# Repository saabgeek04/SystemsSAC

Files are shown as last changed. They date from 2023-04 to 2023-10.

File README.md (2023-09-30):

# Rapid Remote Response Vehicle (RRRV)
This Markdown document details the design process used and the troubleshooting that was involved in creating my RRRV.  
This work was completed as part of VCE Systems engineering Units 3 and 4.  
I wrote this all in markdown for the simplicity and accessability, as well as generally being more pleasant than using word or powerpoint
There are most likely spelling mistakes and grammatical errors in this document spelling is a priority at the moment. I have gone through with a basic spellchecker, but I cannot guarantee perfection.

For my weekly journal, see [here](/journal/WEEKLY.md)

# Overview
## What am I building?
I will be building a remote payload delivery vehicle with a first person view camera. the idea of this vehicle is similar to a bomb disposal robot. Its strength is that it can be used to access areas that are not safe for humans. It will be capable of delivering a payload and navigating complex terrain.  
In more detail, I am going to be equipping my own existing remote control car (Traxxas Slash 4x4) with the equipment needed to drive into an area unsafe for humans so that it can deliver a payload. The car will be run using [Ardupilot Rover](https://ardupilot.org/rover/), and will be able to deposit its payload remotely.  
The payload in question will not be a bomb, I promise. Rather it will be medical supplies or food.  

## Why not a plane?
I'm not designing this for war, but in the event of one, drones and planes can be shot down out of the sky after being picked up on radar. The last thing we want is a urgent and valuable supply drone to fail to complete an urgent mission. A ground vehicle is slower, but could drive along the desert for days on end undetected (and with solar panels too!).  
# Initial Planning and design 
## The Car 
The car is a Traxxas Slash 4x4 VXL
I will be using it as a base, as it has all the features I need and will allow me to focus on the autonomy + Payload. The last thing I need is to be trying to build and diagnose two systems at the same time. The Slash is very robust and reliable, and stands up to large amounts of abuse with ease (trust me, I've tested it). Its also something I am fairly confident with, as I understand it and how it works. Mine has an upgraded steering servo as a bonus as well. 

See [ROVER.md](/journal/ROVER.md) for more information


<i>Picture of the car pre-systems</i>  

## The Autopilot 
I will be using [Ardupilot Rover](https://ardupilot.org/rover/) to automatically drive the car and complete GPS waypoint based missions.  
According to their website:   

<i>Rover is an advanced open source autopilot for guiding ground vehicles and boats. It can run fully autonomous missions that are defined using mission planning software or pre-recorded by the driver during a manual run.</i>

This is perfect for me as I will be able to set up missions around the school to demonstrate the capabilities of my project. 

Documentation for the autopilot side of things will be documented in [ROVER.md](/journal/ROVER.md), as it is all part of designing the rover.

### Background
Ardupilot itself was originally designed as low cost autopilot for remote control aeroplanes and boats, but has also been adapted to run "rovers" as well. Think Mars Rovers. 

It works by acting as a remote control for the vehicle its being used on. It essentially replaces the preinstalled receiver on the "rover". It knows its own position using a GPS module, and connects to a Ground control station for mission instructions and waypoints. 

Overall its a very well sorted system and will make the Autonomous driving part pretty easy (touch wood), allowing me to focus more on the Payload system.

### Hardware
Ardupilot doesn't need much hardware, meaning it will be relatively cheap to install on my car. Below is a brief list of the Hardware I will need:  

- Ardupilot control module
- GPS module
- Telemetry/control TX/RX system
- Sonar/IR for obstacle avoidance (maybe)

See [This Section](/journal/ROVER.md#navigation-computers) for which exact bits I used and why.

### Software
I will be using [Mission Planner](https://ardupilot.org/planner/index.html#home) for my Ground Control Software (GCS) as it is the most supported and popular GCS for Windows. 



As you can see in the screenshot above, Mission planner will allow me to create a set of waypoints which my rover will use GPS to navigate to. Mission planner will also be able to show my FPV camera footage in its HUD if needed, but I could also do a VLC stream if I needed.

## The Payload

See also [Payload System](/journal/PAYLOAD.md)

My initial ideas for the payload so far have been to deliver a cylinder about the size of a 600ml water bottle or maybe a pringles can. The payload will be secured to the vehicle via a custom designed clamping system. I am considering using a seatbelt style strap + tensioner as well, which would allow me to secure multiple types of package. 

### A Cylinder? Why not a box
I am choosing to use a cylinder for a couple of reasons, primarily because they are very easy for a human to hold due to the shape. It also gives me a fun engineering challenge in terms of securing it as it is more complex and less conventional compared to a box. A cylindrical payload could also be transported via other methods, and would be far better for transporting liquids for human consumption (who knows, someone could really really need a bottle of mount franklin!). 
### Securing the Payload

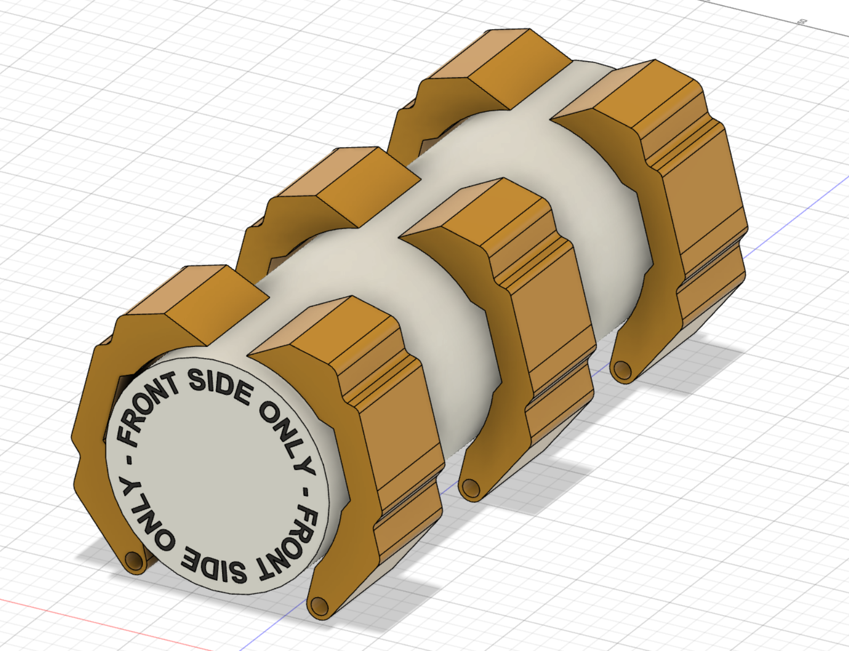
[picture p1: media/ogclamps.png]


I am going to use a clamping system to secure the payload to the vehicle. I want this system to be adaptive to the size/shape of the payload, allowing shapes like water bottles to be held firmly in place. I will have 6 clamping arms along the long side, with another thing at the end to prevent sliding forwards and backwards. The front side will be pressed up against part of the vehicle.

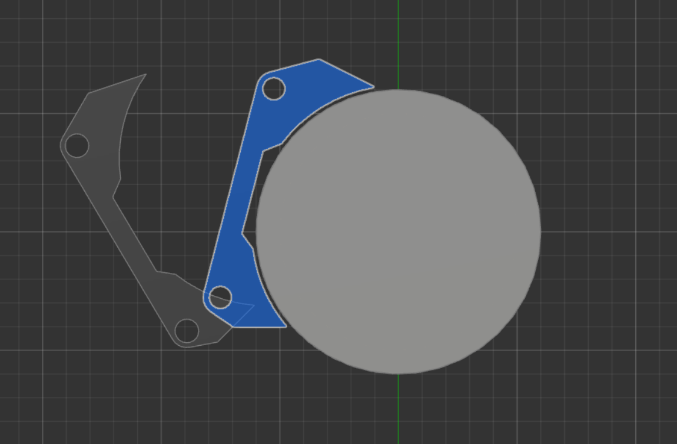
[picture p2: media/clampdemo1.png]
  

<i>Demonstration of initial clamp design and its pivot point</i>

Ideally the clamps can move independently of each other, allowing the greatest flexibility. This does present a problem however: how do I move all 6 (or 3 pairs of 2) at the same time, without needing 
6 individual motors?

I continue the design process for this part in the [PAYLOAD.md](/journal/PAYLOAD.md) document.

## Risk Assessment

As with any project, there are risks involved with the operation of this rover. To help identify and mitigate these, I have grabbed the risk assessment matrix from the [Worksafe website](https://www.worksafe.vic.gov.au/how-conduct-risk-assessment) and filled it in with colours to make it nicer to look at 

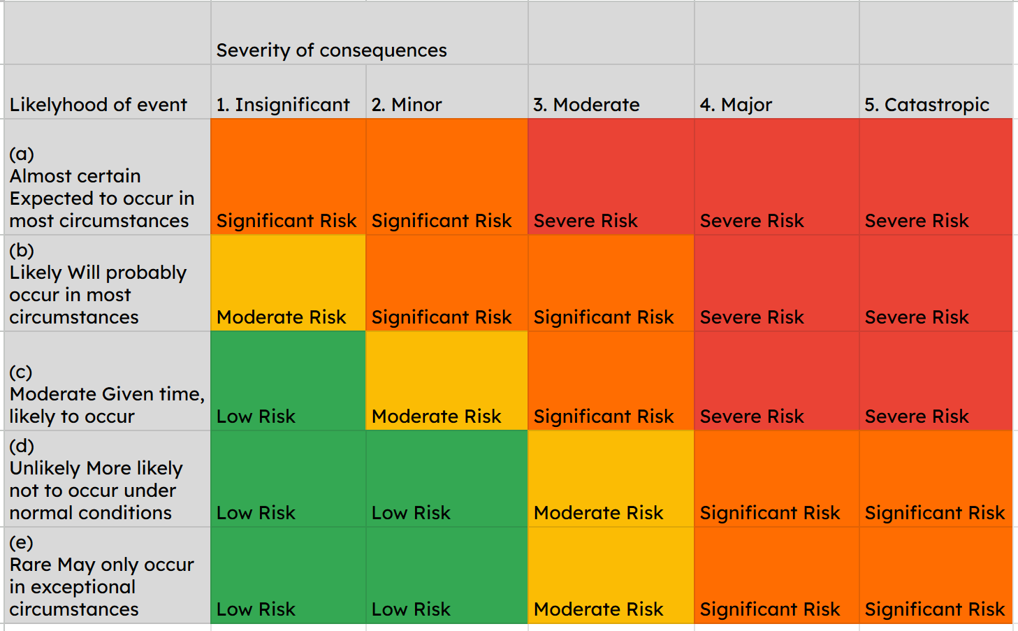
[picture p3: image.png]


#### Key

##### 1. Insignificant
Any injury or disease that needs first aid treatment only.
##### 2. Minor
Any injury or disease that is likely to result in a person being incapacitated from normal activity for a continuous period of up to 7 days.
##### 3. Moderate
Any injury or disease that is likely to result in a person being incapacitated from normal activity for a continuous period of 7 or more days.
##### 4. Major
A fatality or total and permanent disability.
##### 5. Catastrophic
Multiple fatalities.

So, what are some of the risks we might run into? 

### 1. The Rover collides with a person

#### Likelyhood: Unlikely
It would take very strange circumstances for the rover to collide with a human. Humans tend to see it coming and move it out of the way. Unless you somehow dont see or hear it coming (from quite a while away). Its very easy to detect.
#### Severity: Insignificant
I have had the rover collide with me alot. I have sustained less than a bruise from these collisions. It kinda just bounces off your feet.
#### Verdict: Low Risk
A possible solution would be the Lidar sensor to get the rover to avoid humans.

### 2. The Rover Battery Explodes

#### Likelyhood: Rare
The Lithium-Polymer (LiPo) battery used to power the rover is very unlikely to experience thermal runaway during operation. The Flight controller knows the battery percentage, and will trigger a safety toggle to stop operation. The risk really comes from charging the battery, but if the battery is charged on a safe charger and the balance lead is used, then there is virtually no risk of a fire.
#### Severity: Moderate
A LiPo battery explosion is pretty violent. Theres alot of heat that gets released very quickly. If the battery is close to a human whilst charging, then they could get seriously burned.
#### Verdict: Moderate Risk
I believe as long as the LiPo battery is treated with respect, and the user understands how to identify a battery that is at risk, then the risk will be minimised.

### 3. Manual handling of the Rover resulting in back injury

#### Likelyhood: Moderate
Someone in a rush may use improper lifting techniques to lift the Rover.
#### Severity: Minor
Gets worse over time but on a single occurance factor could be unpleasant.
#### Verdict: Moderate Risk
If the correct lifting procedures are followed, then injury will not occur.

### 4. Rover motors activate whilst the rover is being handled, causing harm

#### Likelyhood: Unlikely
It has never ever happened to me, and I've done a bunch of dumb stuff with the rover
#### Severity: Insignificant
The most that would happen is you might get a bit of carpetburn from one of the tires or a pinched finger
#### Verdict: Low Risk
A saftey switch to kill motor power is installed on the rover to prevent this from happening.

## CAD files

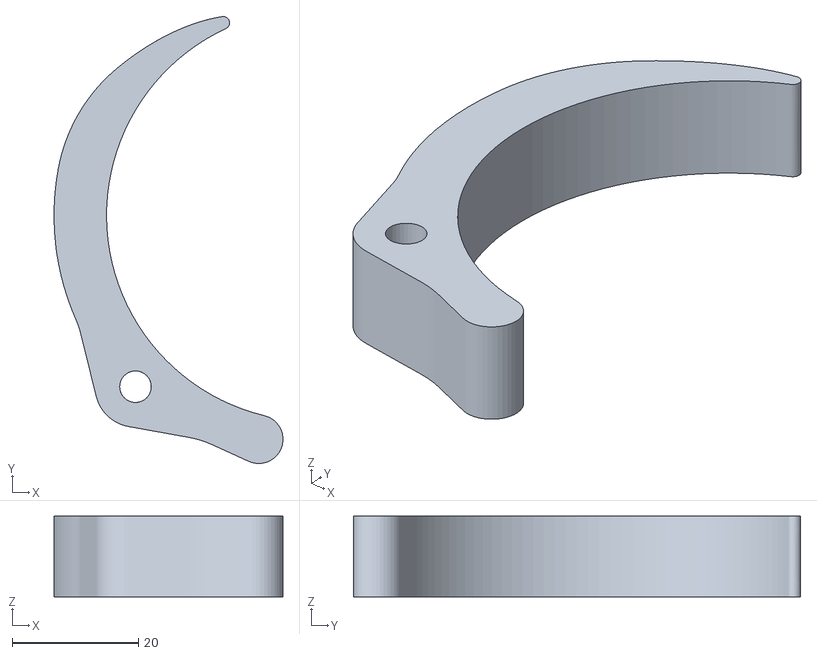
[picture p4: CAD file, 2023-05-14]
3D models/stl/clamp.stl
36.2 x 70.7 x 12.8

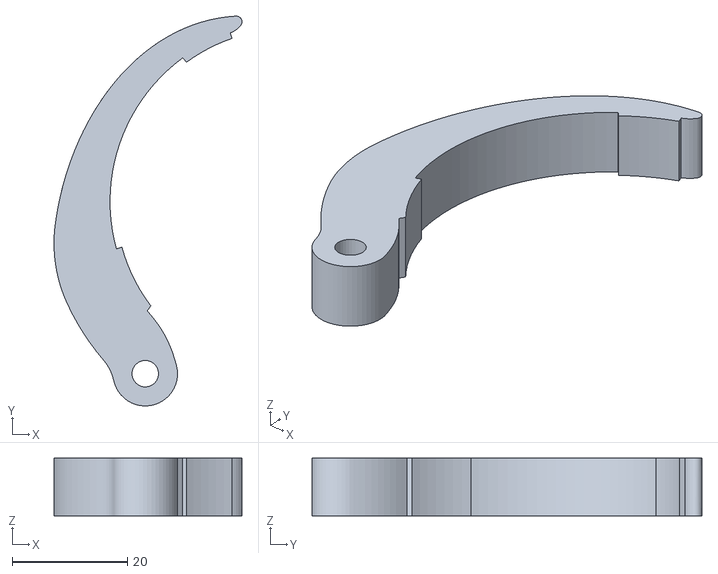
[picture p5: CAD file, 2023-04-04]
3D models/stl/boringclamp.stl
32.7 x 67.7 x 10.0

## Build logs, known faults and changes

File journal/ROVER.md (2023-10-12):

#### [< Back to README.md](/README.md)

# Rover Building
This document details the process I followed to turn my Traxxas slash into a autonomous rover.

## Initial Planning and designs

The Traxxas Slash, like most hobby class remote control cars, has a flimsy plastic body that attaches to the chassis via 4 mounting poles. The body is non structural, and mostly serves as a protective cover, allowing crashes and rollovers to occur without damaging the vehicle. It also has front and rear bumpers, as well as side bash bars, for maximum safety. 

Ideally, All modifications added to the car are completely reversible, "bolt on" modifications.

I initially wanted to mount the navigation equipment in place of the body, via attaching a plate to the four mounting points. I tested this, and found it was not a bad solution. The car drove fine with the plate installed despite the increase in center of gravity, However there are a couple of issues with this design, the main one being that the navigation system would not be protected in event of a rollover, (which would be more likely due to the increase in CG). The other issue is that the body mounts are not designed to deal with the huge forces that I would be creating with all the extra weight.

I then came across this [forum post](https://diydrones.com/group/ardurover-user-group/forum/pixhawk-equipped-4wd-traxxas-slash-chassis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) which basically solves all my problems. 

As you can see in the following images, The navigation systems are mounted on a plate much closer to the chassis.

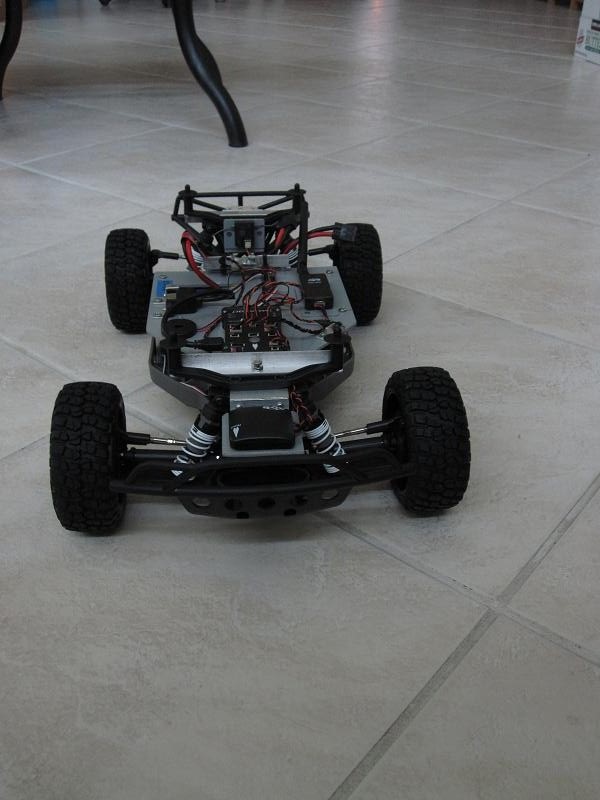
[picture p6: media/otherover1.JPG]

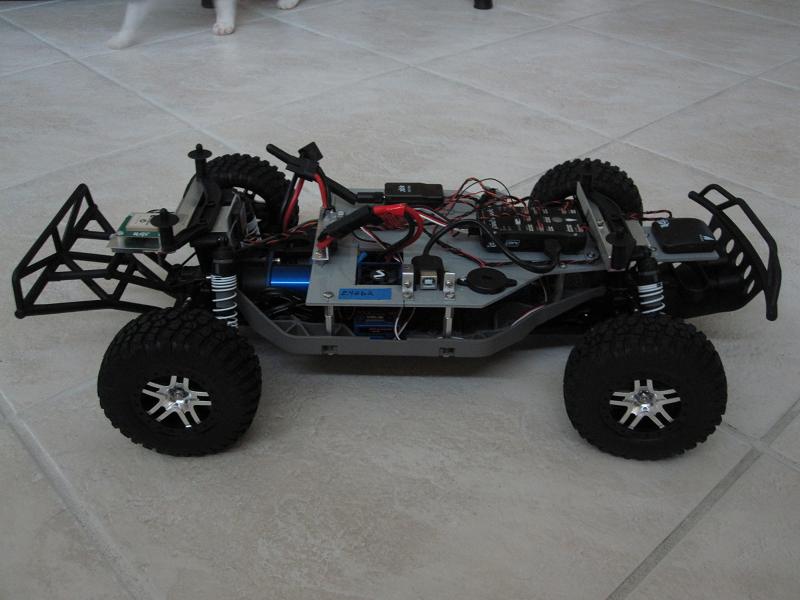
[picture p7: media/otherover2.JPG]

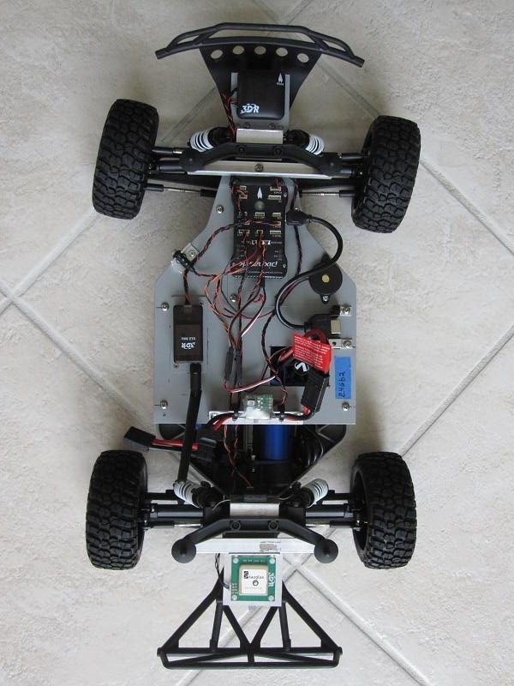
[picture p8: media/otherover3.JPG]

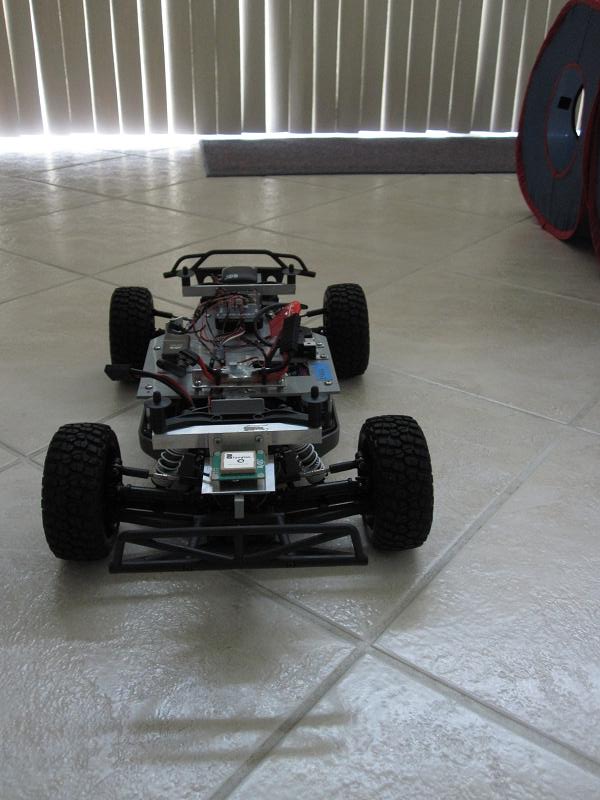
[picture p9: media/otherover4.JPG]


This is a far better design then what I was going for, so Credit to [Thomas J Coyle III](https://diydrones.com/members/ThomasJCoyleIII) for that. 
I will be attempting to reverse engineer these designs so I figured credit was a good idea...

I will be laser cutting the navigation plate out of acrylic, which will mean I can be very precise in the nav mount design. 

I plan to construct two versions, one for prototyping, and one as the final design. This will allow me to figure out exactly which electronics and computers I need without worrying about space on the rover, before constructing the most efficient plate, saving weight and space 

## Navigation Computers

As I previously mentioned when talking about Ardupilot, I needed a couple of pieces of hardware to make my car into a rover

- Ardupilot control module
- GPS module
- Telemetry/control TX/RX system
- Sonar/IR for obstacle avoidance (maybe)

### Which to buy on a budget?

The control module is the bit that makes everything happen. It plugs into the speed controller and steering servo to drive the rover, as well as receiving GPS signal from the GPS module.

The ideal system, if available, would be the [Pixhawk 4](https://holybro.com/products/pixhawk-4?variant=41527199498429), which is unfortunately out of stock and very expensive. Its also a bit overkill for what I need, since I am using a rover and not a drone/aeroplane with complex shenanigans going on.

I started looking for a cheaper flight controller and eventually found a kit on aliexpress that for the price of a regular Pixhawk, would give me all the hardware I need + a Pixhawk clone, as a bunch of bonus bits. [This is the kit](https://www.aliexpress.com/item/1005005167479286.html) and I plan on purchasing the "915V1 1000MWPackageC" Variant. I know I said earlier that I didn't need all the functionality of a fully fledged Pixhawk, but I couldn't really find a better kit for the money. 

This variant comes with a cable that has a voltage regulator built in to power the Pixhawk clone, meaning no cable splicing is required. It also features 1000mw 433mhz radio, which will do the job. 433mhz is not as fast as regular 2.4Ghz, but for my application it will be fine. The 1000mw rating means I will have plenty of range too. Originally I planned to use a 933mhz system, but due to legal requirements I cannot. The power limit for 433mhz is only 25mw ERIP, the ERIP of my radio system is about 100mw, so I'll just turn it down a bit :wink: 

The included GPS module may not be very good, but I happen to have a large box of GPS modules, which were used 20 years ago for mapping and surveying large areas. They are fitted with USB connectors currently, but I can always solder different connectors on if required. I plan to stick with a single GPS unless I start having issues. 

The kit also contains a safety switch (basically a big red emergency stop button but without the big and red parts), a buzzer that can be enabled if the rover is lost and a sd card to be used as a rudimentary "Black Box".

I think this kit, which at this time is on sale for $335 is the best option for me at the moment. Obviously, in an ideal world I would not have to worry about cost and I would just spec out the best solution for this, but I don't have that luxury (Someone sponsor me!) so I'll be doing this all on the cheap, which is kind of the wrong way around if you think about the RC car I'm using as a base. 

There are a couple of other options that are cheaper, but they miss out on certain sensors like a compass, which I may need, and I would hate to order the cheaper kit and need a compass or something else and have to spend more money + time getting a new kit. Once I sort everything out, I will write out a set of minimum requirements so that anyone can spec out a system that works for them for a better price.

## Designing the Navigation platform 

Whilst I wait for the Navigation computer to arrive, I will begin designing the platform for everything to reside on. At this point in time, since I am away, I do not have access to the car itself, but I have previously measured out parts of the car that I can then combine with an arial shot of the car to get approximate measurements. When I return home I will be able to take some more precise measurements of the car to further refine the model. I know that I am not the most precise measurerer, so I will build in adjustability in form of some slots. I will also cut prototypes out of cardboard to make sure everything fits properly without wasting material (a mistake I made previously...oops)
To create the initial plan design I traced a top down photo of the rover chassis, not very precise, but I can tidy it up later

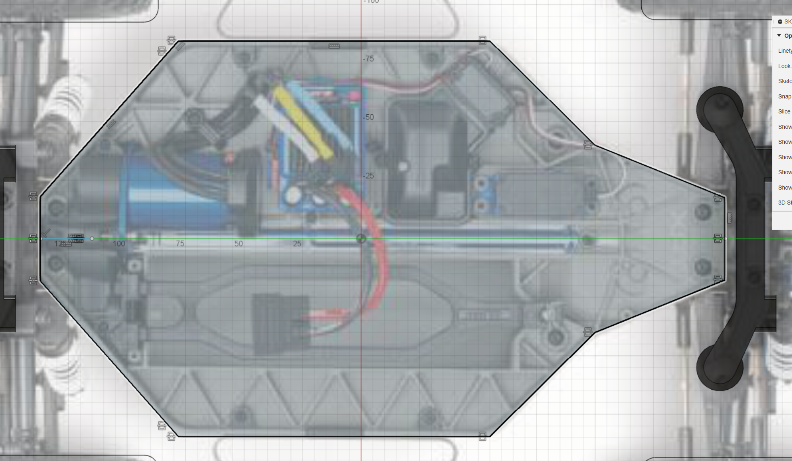
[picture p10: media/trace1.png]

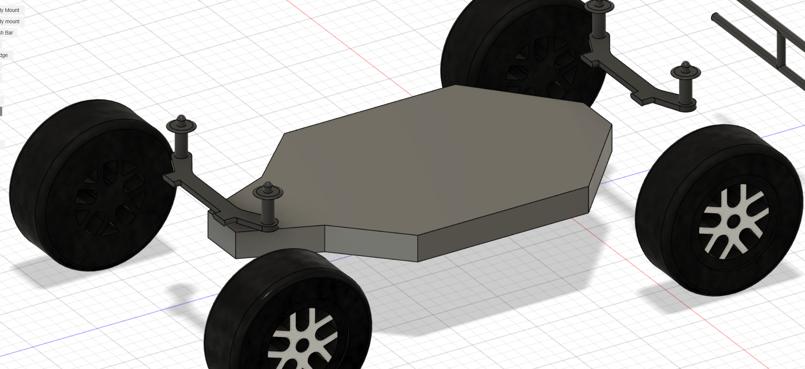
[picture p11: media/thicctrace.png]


I did this on the same document I used to make [this acrylic plate](/journal/WEEKLY.md#23rd-february) as the measurements for the body mounts were somewhat accurate (+-1.5mm). When I have access to the rover in person again, I will be able to measure out the length of each side and draw a new sketch to suit.

There are alot of different forces at play during rover operation, and I want the computers to stay relatively safe during this. I expect to hitting lots of bumps and other obstacles, and even if I do upgrade the suspension, theres only so much it can do to smooth things out. The primary computer comes with a anti vibration mount, but the rest of the stuff does not, fortunately, we can 3D print TPU (a kind of rubber), which I will use to make rubber "washers" that will soak up a decent amount of vibration.

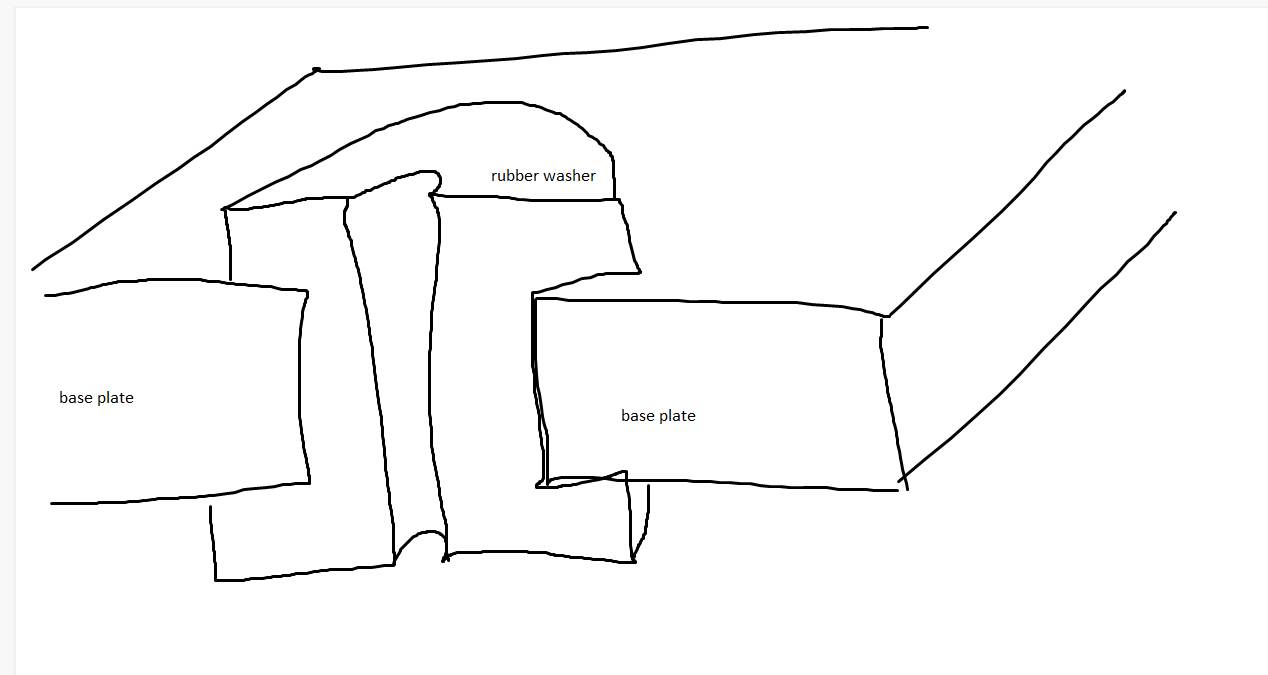
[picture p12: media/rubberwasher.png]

<i>an expertly drawn cross section of the rubber washer design</i>

When I got back from WA, I measured out the exact(ish) dimensions of the chassis, which was difficult without removing parts of the car but I managed to do it.

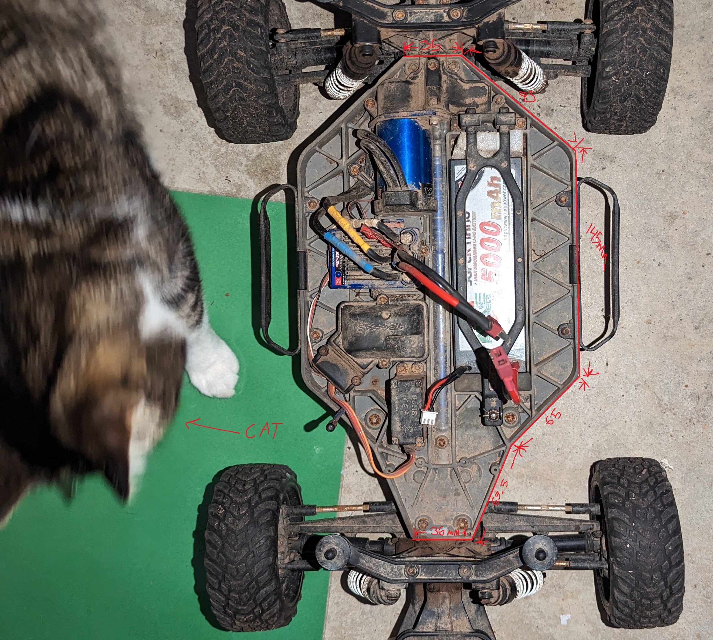
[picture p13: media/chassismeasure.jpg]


Its not the greatest of photos, but it doesn't need to be either.

I struggled to get everything to line up, but then I got the width and length measurements and that helped alot with sorting out everything. I wasn't sure what angle the 65 and 63.5 bits were on, so I made circles with the same radius and used the intersecting point of those two circles, which worked very well!

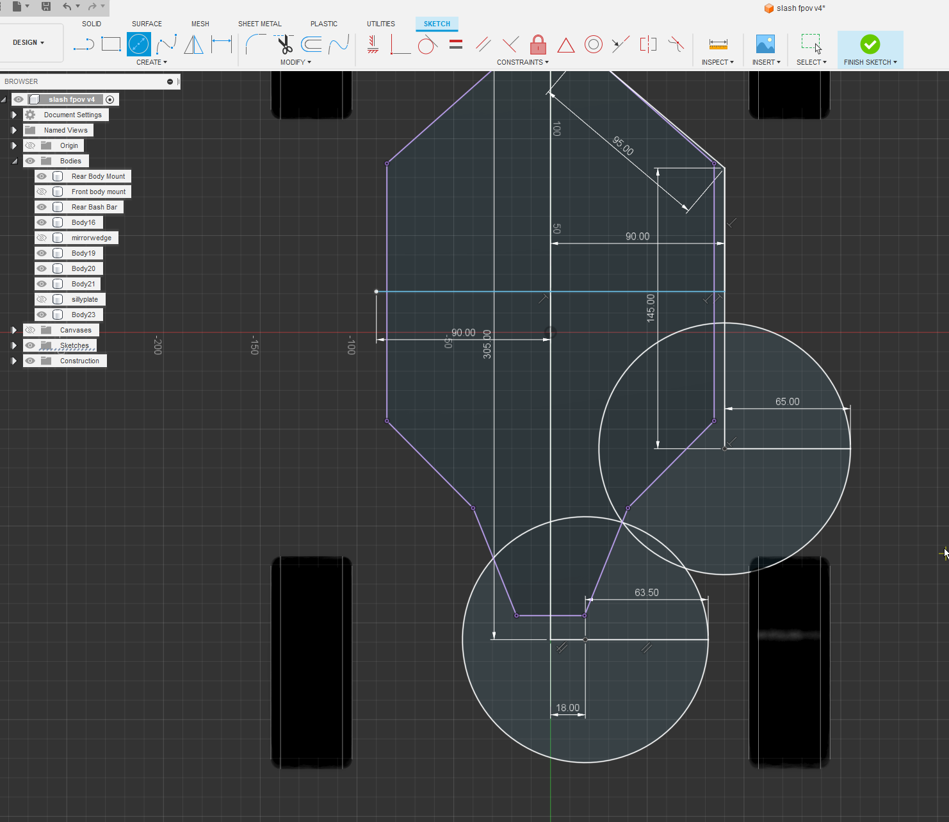
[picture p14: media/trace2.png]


In this next image, the blue is the old one and the grey is the new one, as you can see 

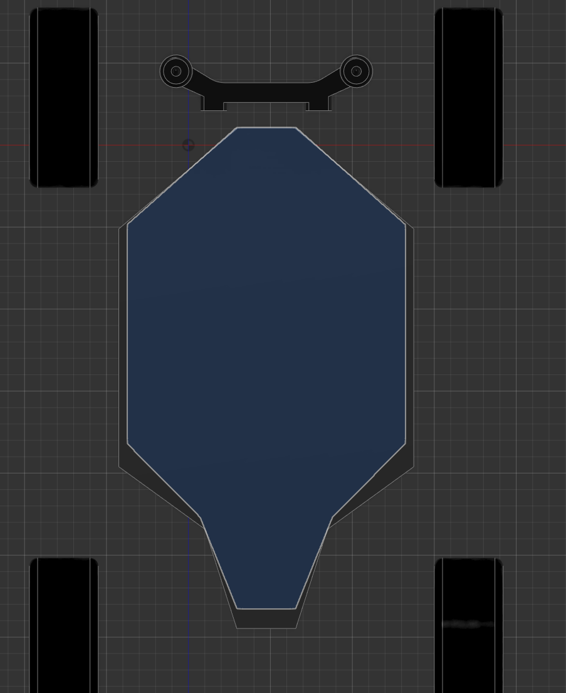
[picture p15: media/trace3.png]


In class, I cut this trace out using cardboard, and no suprises here, it didn't fit properly. I went through 5 iterations, every time getting closer and closer to perfection. I still need to make the 5th piece narrower at the back, that way I can accommodate the suspension. The laser cutter we have is amazing for rapid prototyping in this instance, as I can cut, review and redesign over and over, all using cardboard that would have otherwise been thrown away.

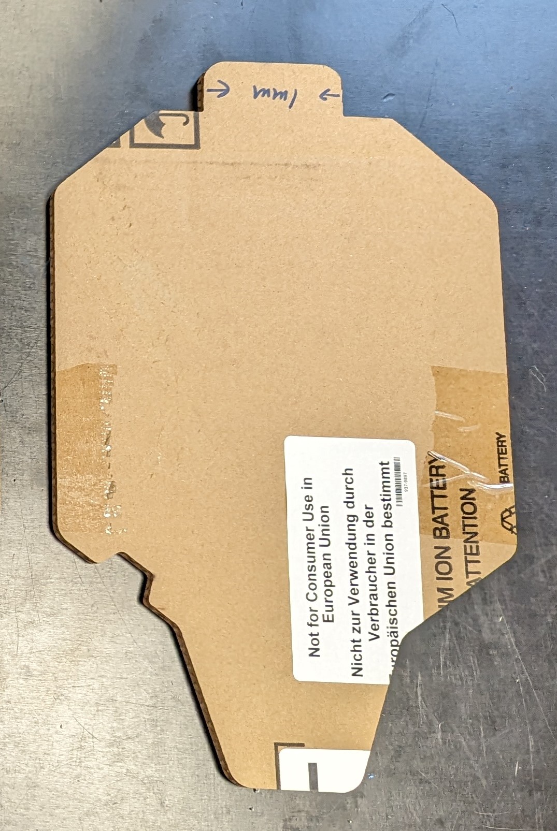
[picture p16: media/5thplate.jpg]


## Flight controller setup and usage

Getting the Pixhawk working was pretty easy. It seems complex initally due to the amount of stuff going on, but once you understand everything its not bad at all. 

[](image-1.png)

<i> A diagram showing all the devices connected to the pixhawk</i>

When I got my pixhawk, I was instructed to put particular firmware on it, so I did, and it didnt work at all. I put the latest firmware on it and it started working. There wasnt much else to do except mount everything. Most of the stuff I had to do to get it to work properly was PID tuning and Motor Calibration. 

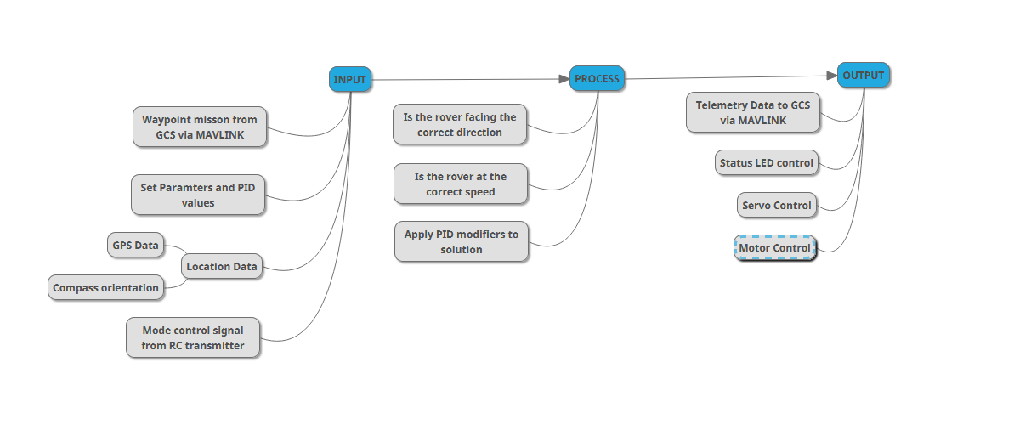
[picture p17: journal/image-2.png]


## Complete Redesign

I realised it wasnt super efficient or really worth mounting everything on a single plate, and I also wasnt happy with the mounting system at all. I made up some parts in fusion360. The idea with these was to make my mount alot stronger and less wobbly, reducing stress and enabling me to mount things better. 

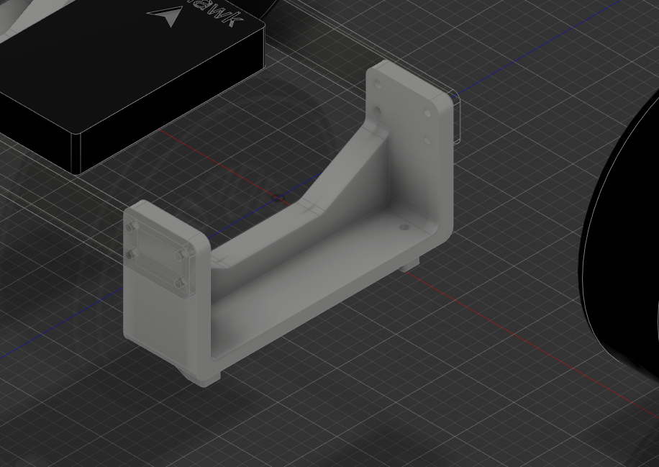
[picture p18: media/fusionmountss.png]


I then 3d printed these pieces, one at a time due to the dubious reliablility of the 3d printers. 

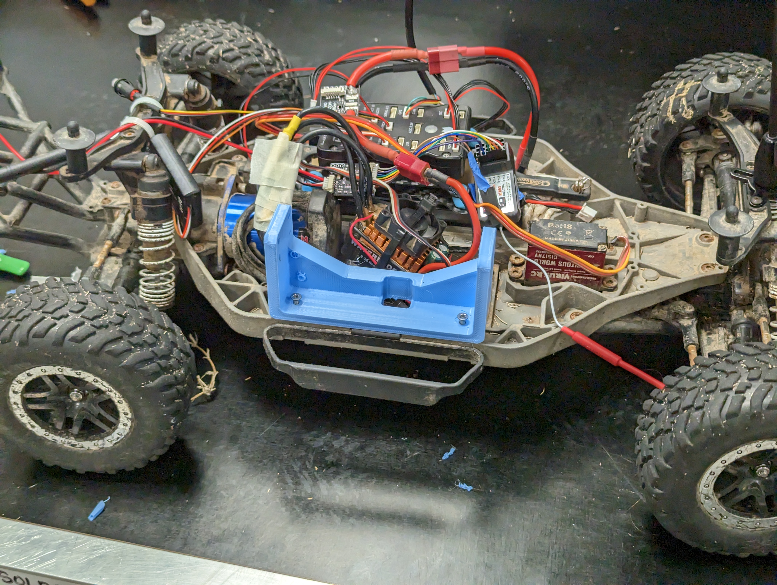
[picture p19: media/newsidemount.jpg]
  
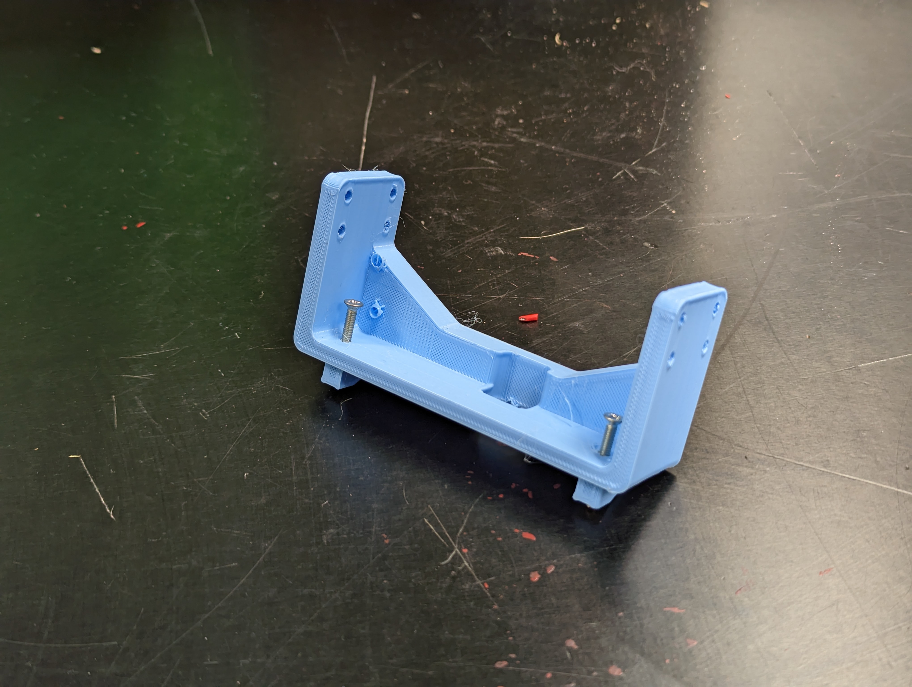
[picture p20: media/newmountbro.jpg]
  

Notice that the reciever and ESC just floating around in the car. I ended up making a mounting plate 

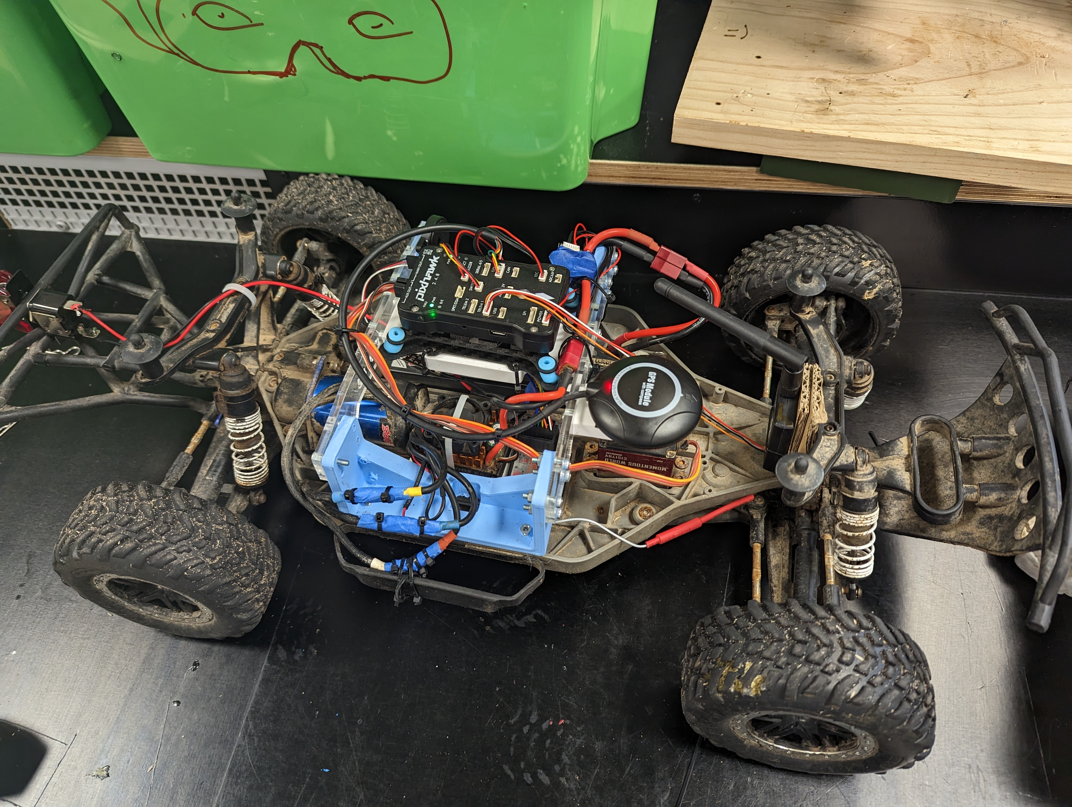
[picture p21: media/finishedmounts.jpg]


This week, I finished printing the other mount and laser cut some cross braces. I built holes into the cross braces, that way I could mount the pixhawk and I also lowered the GPS. I was initially concerned about the GPS getting less reception due to being down lower, but in practice, this was not the case. On occasion, I noticed I had one less satellite, so no really huge difference there

I also mounted the speed controller and reciever much lower and properly wwith 3M DualLock velcro tape, which works really well.

After some brief testing, I found that I needed to make some mudguards to stop grass and mud entering the rover. I prototyped some parts out of cardboard, which worked pretty well and got rid of 99% of the debris, but the cardboard was not going to last very long, see below:

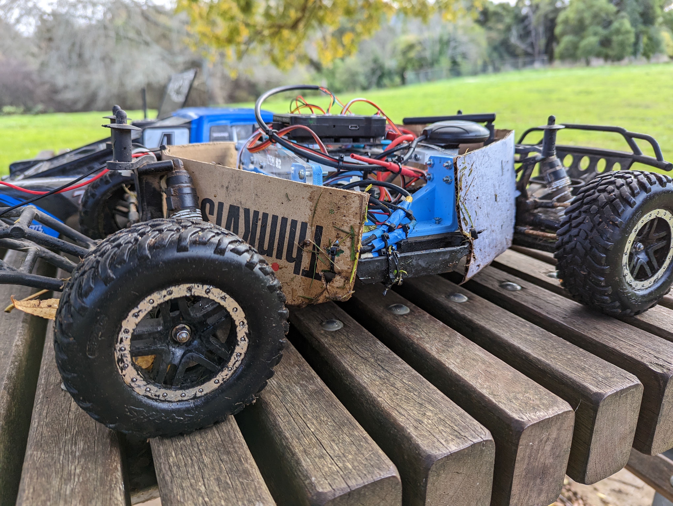
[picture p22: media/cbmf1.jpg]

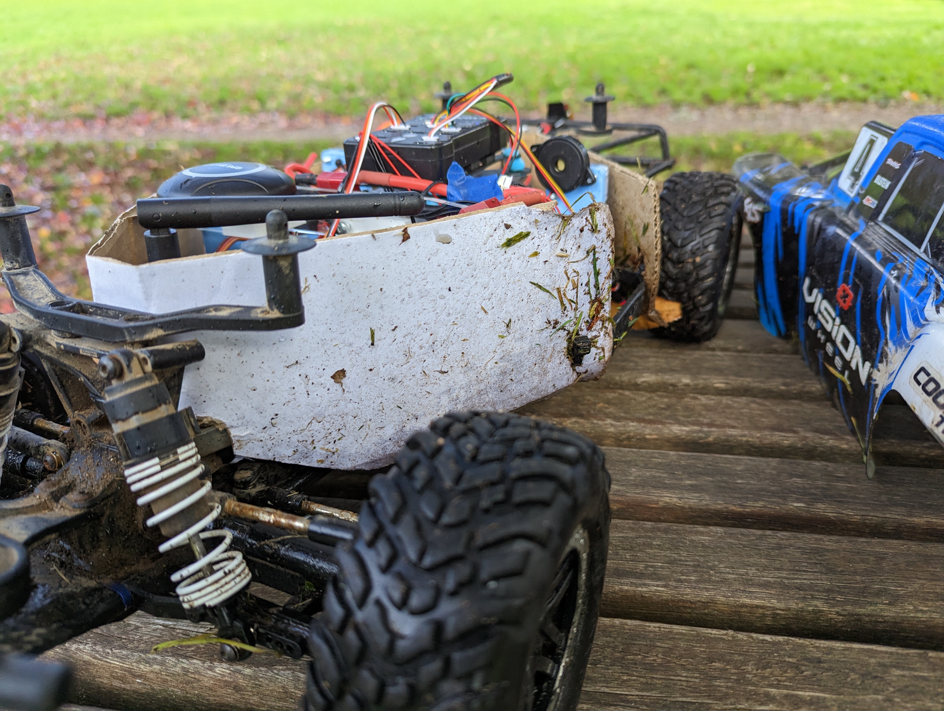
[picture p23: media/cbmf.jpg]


To fix this, I made some new parts out of coreflute. These look much cooler, and dont get saturated when used in water. I still have some water hitting the underside of the "cabin" portion of the body, and this can cause water to drip down into the "isloated" space where the electronics are, so I am going to look into getting a waterproof mesh cover or something similar. If I wanted everything totally waterproof, then I would probably put everything in a tuppawere container, but this is not a boat, so I should be fine.

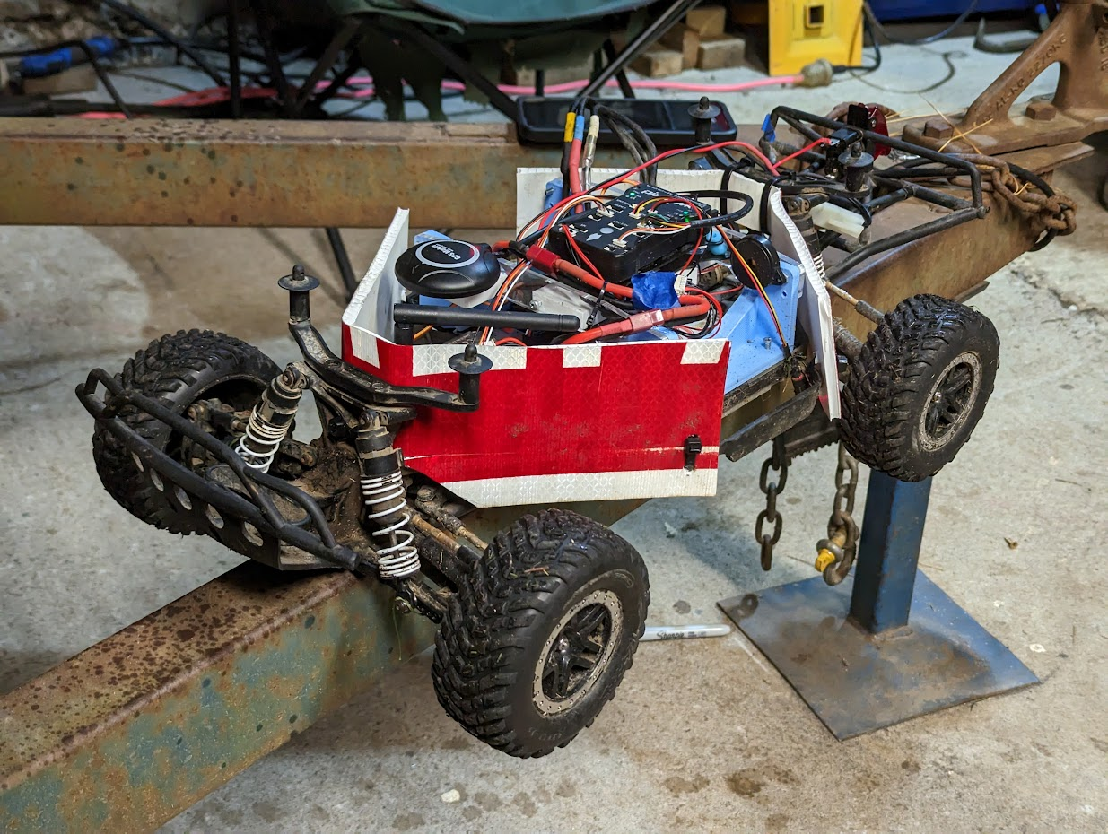
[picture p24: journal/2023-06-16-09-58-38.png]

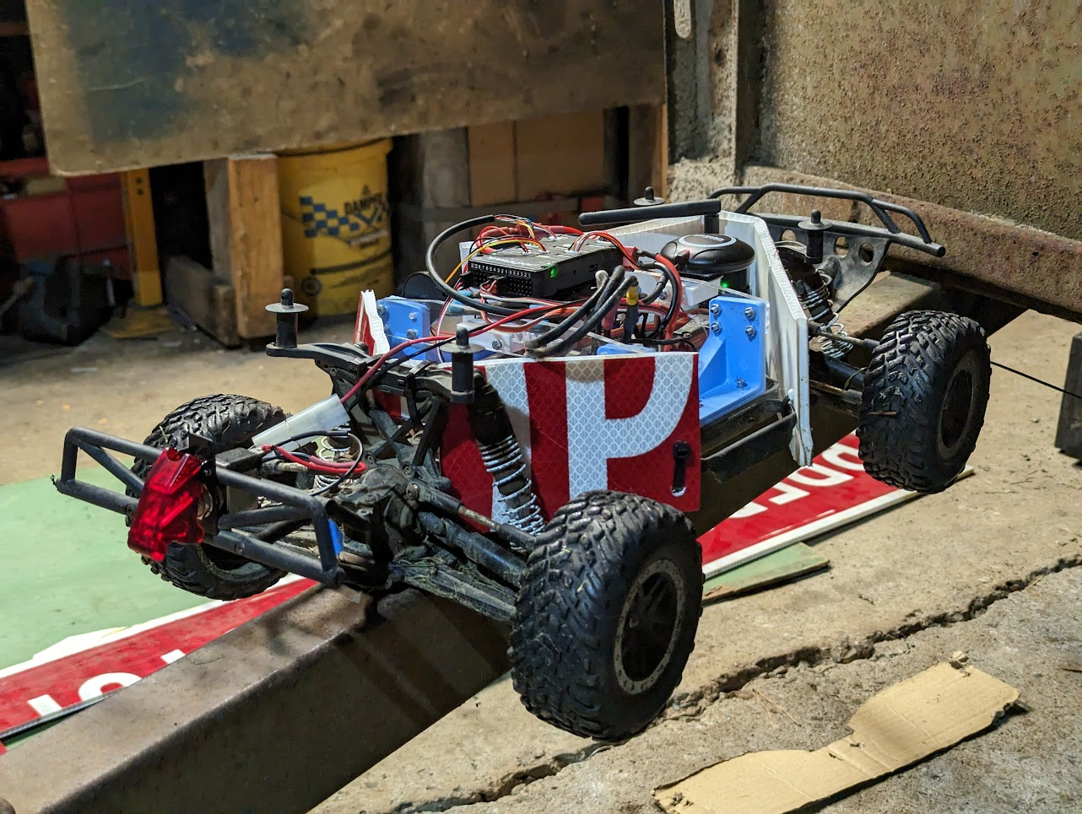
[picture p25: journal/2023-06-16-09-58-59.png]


This was also done on relatively tall, wet grass, which is difficult for a whole host of other reasons.

### Final layout

Heres a little collection of photos showing the final layout of parts on the rover

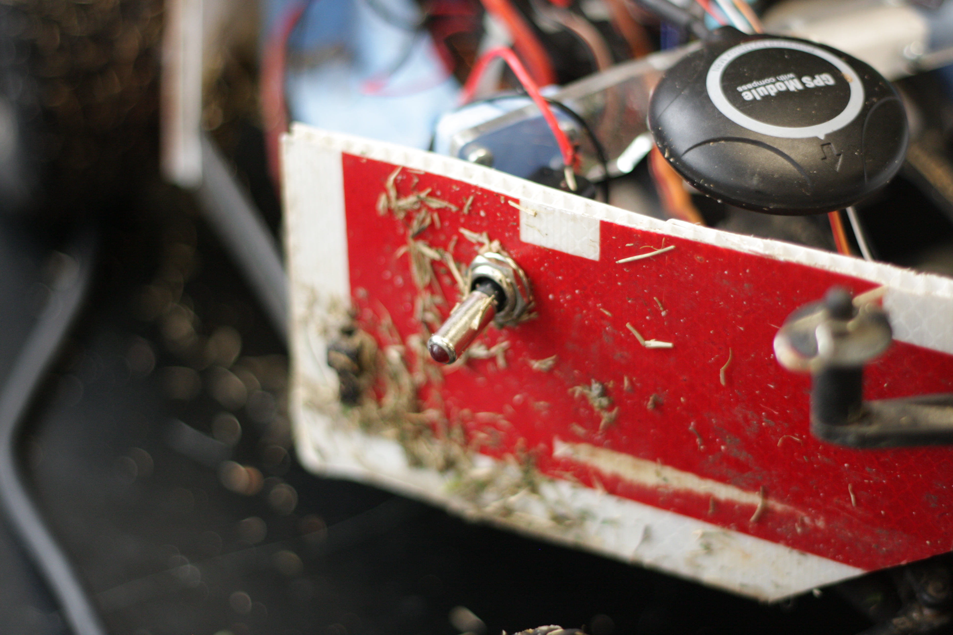
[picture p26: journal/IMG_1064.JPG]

*The GPS and Motor Shutoff Switch*

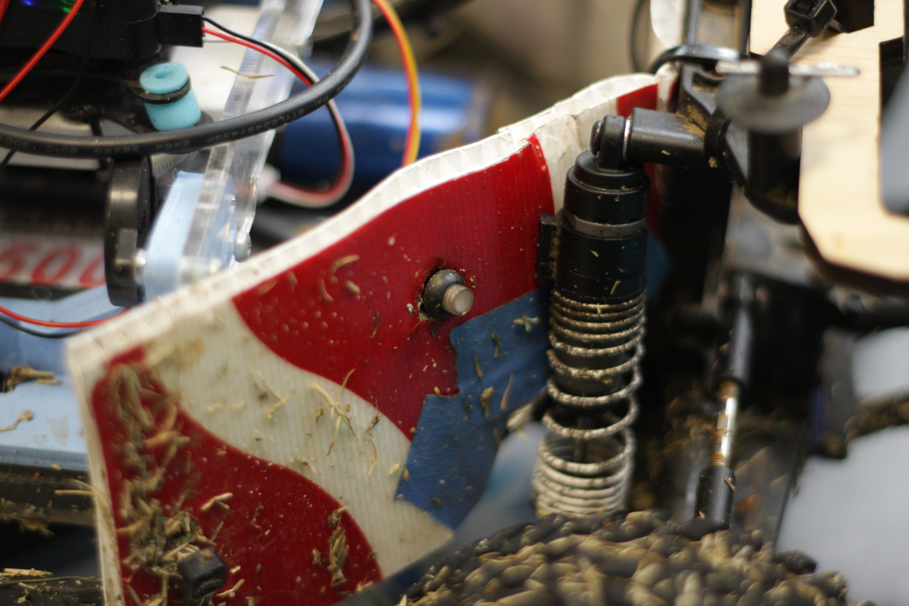
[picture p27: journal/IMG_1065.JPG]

*The Safety Switch at the rear of the car*

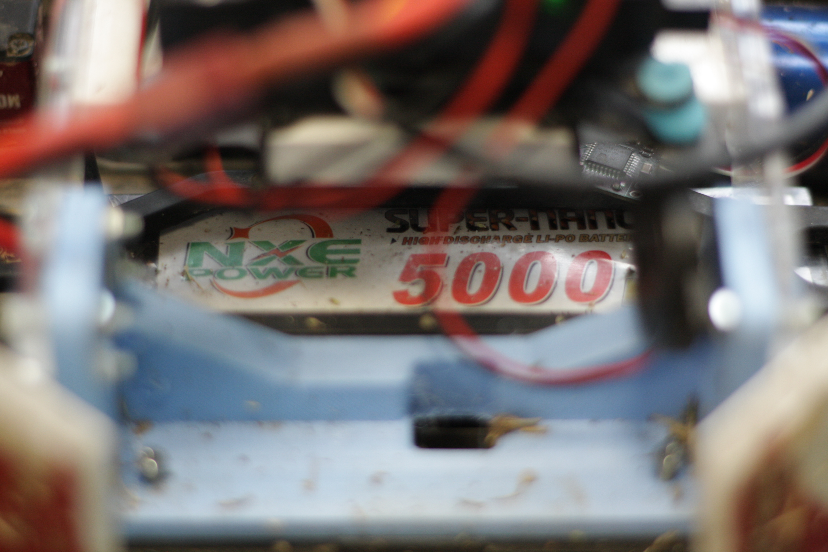
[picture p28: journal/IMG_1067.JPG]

*The battery tucked away in its compartment. At the top-right, you can see the PPM encoder*

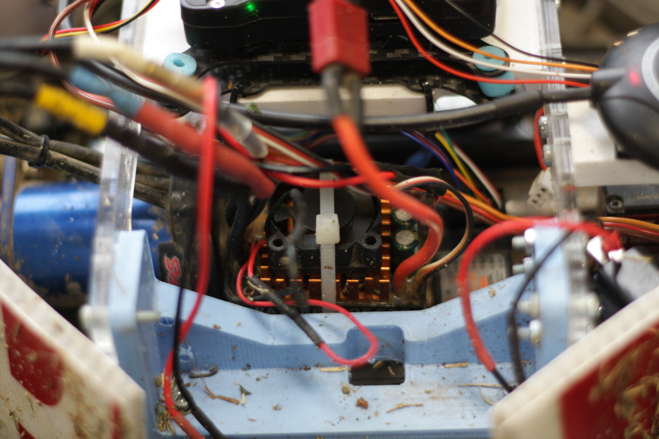
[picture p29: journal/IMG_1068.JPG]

*The Electronic Speed Controller (ESC)*

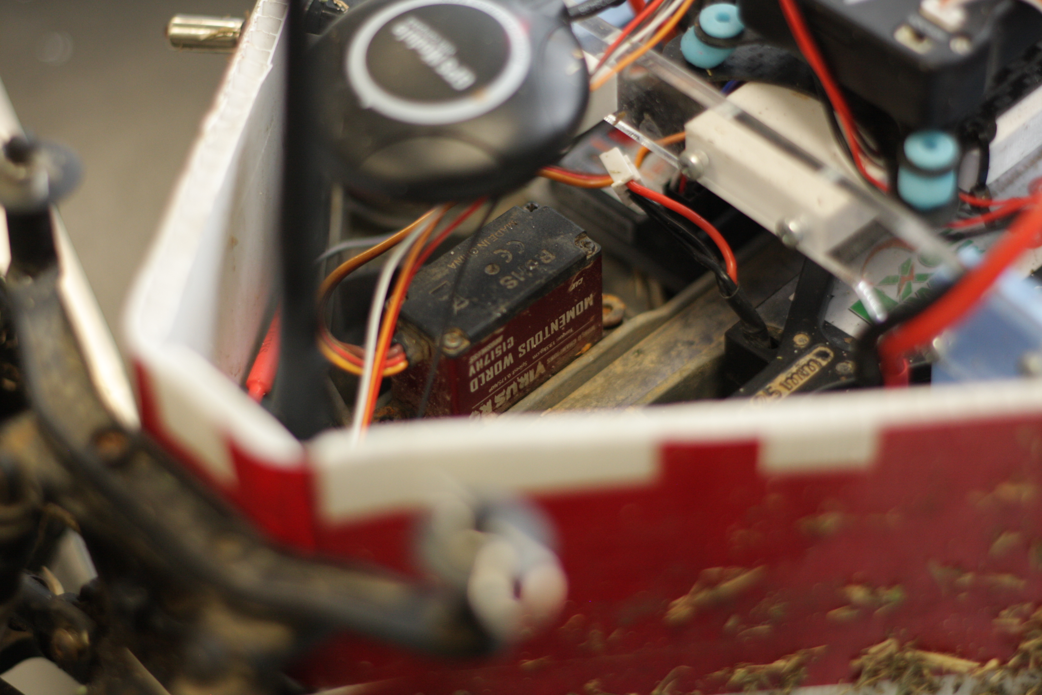
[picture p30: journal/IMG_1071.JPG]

*The Steering servo sitting up front*

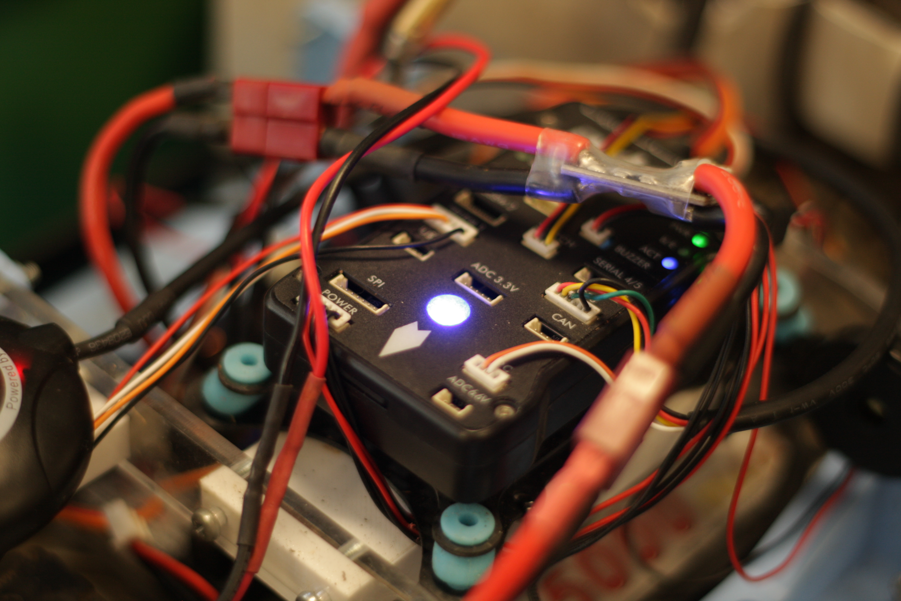
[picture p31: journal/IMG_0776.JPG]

*The Pixhawk, I.E the brains of it all*

## Lightbar 

I really wanted to have a lightbar that woudl show me some status lights as well as work as navigation lights at night. The Ardupilot actually has support for profiLED and neopixel LEDs, but if you wanna do fancy stuff with them like I do, you actually need to write some lua scripts. I am by no means any good at programming. To date, the most I've done is make a javascript... script? that rotates a window on a website to face the cursor, very similar to a steam trading card. 

I looked at some example code, and with the help of a much more skilled friend, went through and we tried to make a script that would work. After about 4 hours of troubleshooting, much refactoring and 2 new wiring harnesses, we gave up on profiLED.

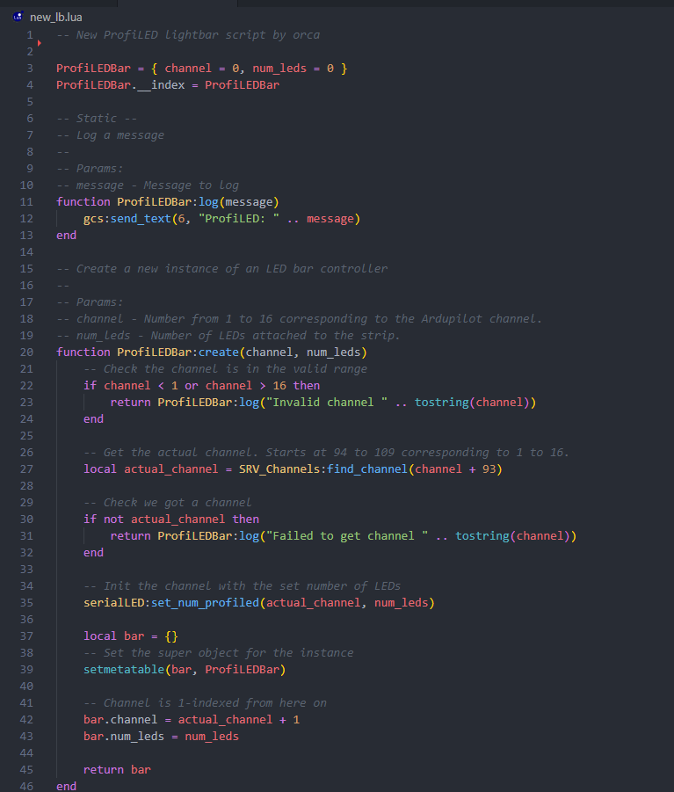
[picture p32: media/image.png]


<i>part of the code we wrote</i>

I then tried using Neopixels instead, but could not get any output out of the Pixhawk at all.

## Obstacle avoidance and LIDAR

I had a little budget left and really wanted to have obstacle avoidance, so I spent $80 and bought a TF02 Lidar sensor off aliexpress. It suprisingly only took two weeks to ship, and when it arrived I had to repin it, but once that was done I plugged it in, set the relevant parameters and.... nothing. It was getting pretty annoying having nothing new work with the Pixhawk, sooo...

## Firmware

It was at this point I decided to reflash the firmware on the pixhawk. I backed up all the parameters and reflashed Ardupilot rover onto it. This fixed nothing. This kinda sucked. I had a look at other options for Pixhawk firmware as well as different GCS (ground control software). I landed on running PX4 firmware (as opposed to ardupilot, which I was previously running) and using [QGroundControl](http://qgroundcontrol.com/). This combination seems to be more of an industry standard(?) and is the "it just works" solution compared to ardupilot, which is more of a hobby class solution. I haven't started on getting LIDAR or the lightbar working on Qgroundcontrol, but currently, I'm happy that its just working, and the user experience on Qgroundcontrol is much nicer than Ardupilot. It's highly likey that my issues with LIDAR and NeoPixel are due to me purchasing a flight controller off aliexpress, but its worth trying all the software first before I come to that conclusion. 

## Ground clearance

You may have noticed that the rover sits pretty low, which is great for handling and driving at speed, but I found that now that I have a payload on the vehicle, the rear sits way too low, and over bumps can hit the ground pretty hard I rebuilt the rear shock absorbers to help with this, (I may or may not have blown them out at the skatepark last year and forgot to put new oil in them...). I initally put a blend of 10w and 85w oil in to try and achieve something close to 45-50w, which is whats reccomended for this model, but this ended up not being quite enough. The thicker the oil in a shock absorber is, the slower it moves. I ended up putting 85w in for this reason, as well as moving the shocks into a more vertical position, meaning that the rover was nice and high off the ground.

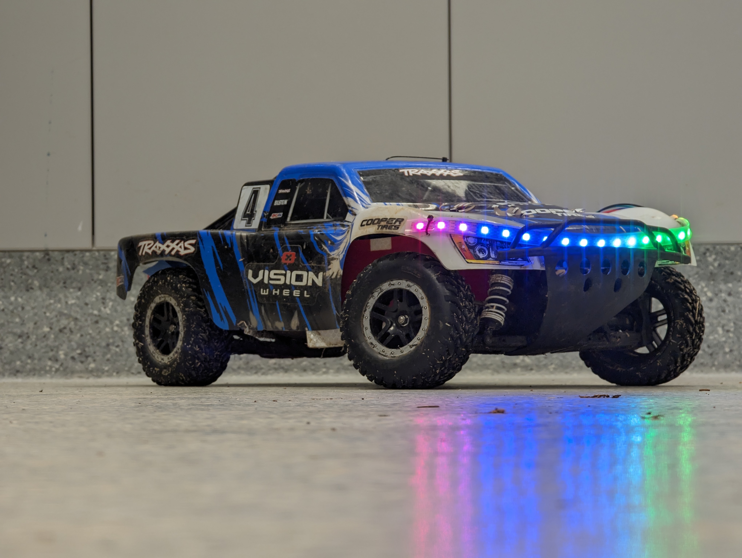
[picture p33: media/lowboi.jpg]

<i>Old suspension config, No Payload... when the profiLED bar kinda worked</i>

#### insert images here of new suspension.

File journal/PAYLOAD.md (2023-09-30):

#### [< Back to README.md](/README.md)

# Payload Clamping System
This document details the design process I used to create the Clamps system that will secure my payload. 

## Initial Designs 



I designed the initial clamps whilst on a plane to western australia, and all they really do is grab the payload and pull it down. They were very simple clamps but they worked, somewhat. I was sitting next to my dad on the plane, so him and I discussed the clamps and their shape quite a bit, and we started focusing on shape optimization.

With my dads recommendation I removed as much excess material as possible to create the most barebones clamp possible, then I can make it look pretty once I know all the design constraints. 
Using a stress test we can see that there is not much, if not very little wasted material.

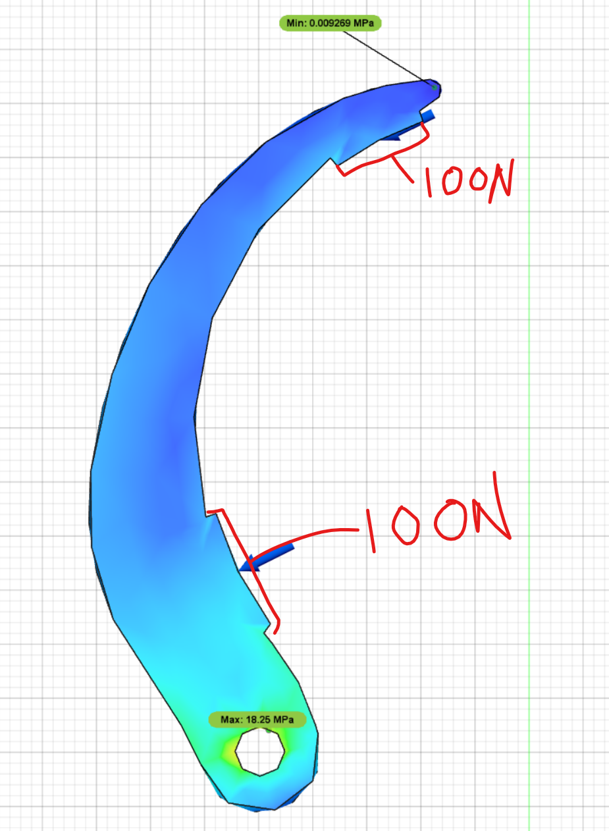
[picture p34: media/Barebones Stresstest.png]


You can also see in this image that just around the pivot point there is significant stress. Ideally when I complete the design it will have two points, allowing for better load distribution. I will also add some extra material if required... we will see...

The other issue is failure modes. Ideally, the clamps fail shut so that the cargo is locked in place until it reaches its destination, where, upon arrival, it can be removed via a manual override. If the clamps were to fail open whilst the car was driving then the payload could be lost, which would mean mission failure

Steering servos use gears and can be moved pretty well by hand, but ideally I don't need 6 of them, and If I did have 6 they would have to be relatively powerful to keep the payload secured. I could also use a set of very small linear actuators, however that would be incredibly complex and silly, as well as very hard to override manually As an engineer, I am required to find an incredibly simple, "why didn't I think of that before" type solution. I think said solution will most likely involve springs in some way.

# Design Process 

I started by thinking about the motion I want the payload to follow when it is loaded and unloaded, and realized that I could get the clamps to follow the payloads motion via pressure, The idea being that the payload pushes the clamps themselves as it goes down, and then the payload can be further locked in place, whether thats via a manual switch or an electronic one, I don't know yet, but it will be whatever suits. I probably don't need to have remote control over this, but that depends on how well people react. Some collaboration with the psychology students may be an order.

## Automatic Mechanical Clamping 

Hopefully the following screenshots help with understanding the motion I intend for the clamps to follow.

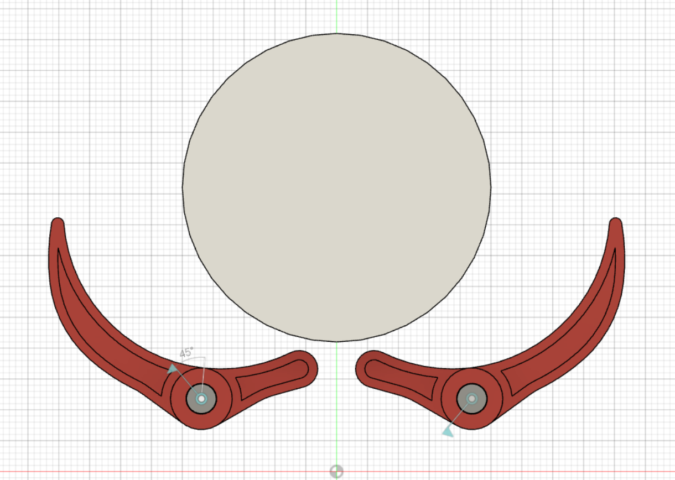
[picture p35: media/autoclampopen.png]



To test this idea, I will need to construct a prototype and see how it performs.

To start with, I will be using a half length pringles can as my payload, as it is pretty close in size to what I envision my payload to be, and its something I have access to right now and can easily get more of. I can also use the contents of said pringles can to keep myself motivated and continue to work on this project.

To begin with, I modelled the can in Fusion360, my weapon of choice for designing this project. I get a free license through the education department, so I may as well. 




Designing the pringles can was pretty easy, it's just a cylinder after all

I then scaled up the clamp I designed previously to match the new size of the pringles can, as well as further refining it to secure the payload better. 



I initially wanted to make 6 clamps but I deemed that would be too much for just the prototype, So I ended up just making 4 instead. I probably only needed to make one pair of 2, but I want to make something a little bigger. 



I also added some 3mm thick plates for the whole thing to sit on, that way I can sit the prototype on my bench and test it, rather than trying to somehow hold it in place and manuever things around. It was also around this point I realized Fusion360 had a high DPI mode (in the beta/experimental features section), which is very cool and will mean my screenshots from this point onwards will look alot nicer!



# Revising it all

I 3D printed a prototype of this system and realised that it was overly complex and very inflexible. I opted to swap it out for a more conventional design instead. This would make the payload easier to mount, able to be mounted lower down in the rover and have far less failure points.

## Design

I went with an easier to recognise and familiar medical supply box 



I started off by modelling it in fusion, and then making it openable and able to be locked shut.


I then scaled it up a bunch and 3d printed both the body and the lid

#### insert images here

I laser cut a holder for the medkit and mounted that on the rover. I also cut up the body a bit to make some space for the lid.

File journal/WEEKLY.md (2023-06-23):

#### [< Back to README.md](/README.md)

# Systems Weekly Journal 2023

## 23rd February  
I managed to find some spare time during the class to laser cut a prototyping plate for my project, however it was a little too thick. however I am not sure if I will be able to make them any thinner due to flex. Next period, I will test how much the plate (made of acrylic) will affect the center of gravity of the vehicle



## 24th February
I tested the the acrylic plate on my remote control car, and once I made it fit (Kind of) It stayed on the car through some low speed testing maneuvers without much increase in body roll. When a weight was placed on the car, the body roll was amplified substantially, but the car remained planed -the suspension did its job.

#### Between here and my next entries not alot of work was completed due to us learning about other concepts including AC power and transistors
#### On the 26th of March I started writing my folio in this repository instead of Simplenote as it turned out not to be well suited formatting wise

## 1st of April through till 17th April
Whilst I have been on holiday in WA I have been doing bits of work here and there to catch up and hopefully get ahead a bit.

Whilst on the plane, I prototyped my initial clamping system design in more of a prototyping sort of way, allowing me to sleep on my idea for a couple of nights and then come up with my current design a little while later. I then started working on figuring out which navigation computer I was going to use, and eventually found a kit that will talk to my systems teacher about purchasing (not with my systems budget however...). After this, I began designing a rough drawing of the baseplate, which I will improve upon once I get home. I will also plot out where the standoffs will screw in and stress test the whole thing so that it can withstand rough driving.
co
## 3rd of May 
At the start of this week I ordered the navigation computers. They will arrive by the 22nd of May, apparently.

I started prototyping the navigation platform, via means of cardboard cutouts, allowing me to get the dimensions perfect and deal with any obstructions that I would have run into without, like the 2.4ghz antenna and the rear shocks. 



I also 3d printed my clamping arms meaning I can construct my clamp prototype after I finish building the navigation platform. I am prioritising the navigation platform so that I when the computer arrives I am ready to install it, And I'll use the time inbetween to work on the clamping system. I also need to finish the navigation system first so that I can decide where and how the payload system will be mounted. 

## 10th of May
In this session I started redesigning my body mounts to account for the fact that I did not have long enough standoffs. This is not an ideal solution, but it will have to make do. I does have the side effect of allowing me to mount ports underneath the navigation platform, which is helpful.

I laser cut two of these mounts without checking if the other side would fit, and suprise! it did not. I did not have enough time to finish these clips, so they would have to wait until next session.



## 17th of May

I finished prototyping and building the navigation platform mounts, which is great because I was able to finally put the mounting holes in the navigation platform. I will be able to laser cut the navigation platform next week (or later this week if I'm lucky...) and I will be ready for the computers to arrive, which is very exciting! According to AusPost, they should arrive tomorrrow or the day after, which will mean that if I have the time I could probably get them fully operational by next week. 

## 18th May through till 22nd

The parts arrived, and were packed relatively well. Everything I ordered was there and on the 18th, I began setting up the autopilot system. The first issue I had was "NO GPS", which was caused by the fact that the GPS module that came with my kit was fitted with a diffrent connector than the one required. The pixhawk wanted a 6 pin connector, but my GPS was equipped with a 5 pin. This is actually normal for this particular GPS, and it comes with a 6 pin connector, so I followed [This tutorial](https://www.youtube.com/watch?v=6nLe9_2Fyok) and repinned it, which worked perfectly. 

The next day, I added all the parts to my rover and took it outside, where I let it gather GPS data for a bit. I wasn't really looking for anything in particular, it was more just proof of concept 



### GPS accurracy 

I managed to get GPS accuracy down to about 4m, which isnt too bad, but ideally I would manage to get it down further. on a large scale mission, it doesnt matter too much, but it would be nice to have more precision, which I might be able to achieve via differential GPS, which is what is used on farms to get accuracy down to the centermeter. Using a usb GPS plugged into my laptop, with my laptop in a known location, then I could use [This Ardupilot Module](https://ardupilot.org/mavproxy/docs/modules/DGPS.html) to achieve much greater accuracy. I would like to get down to 1 meter if possible , which would mean I could do laps of the school oval, or even navigate around the school. It would mean I could also drive the rover on single laned road sized paths and stay on the road at all times, which would be great. I am unsure how good the native DGPS would be, and I have looked into finding a free DGPS subscription, but with no luck. I have enabled [SBAS](https://www.amsa.gov.au/safety-navigation/navigation-systems/satellite-based-augmentation-system-sbas) which has given me much more consistent GPS data as seen below

  

<i>no SBAS</i>

  

<i>SBAS (media coming soon, when I was testing SBAS it started raining and I had to recover the rover)</i> 

As you can see, the addition of SBAS has improved the amount of drift significantly.

### Return to Scheduled Programming - Trying to build a rover

Later that night, I started trying to get the rover into a state where it would be able to drive itself. The pixhawk itself does not support [PWM](https://en.wikipedia.org/wiki/Pulse-width_modulation) inputs, but thats what my remote puts out, so I had to use a PPM encoder, which came in the kit that I bought. The encoder actually runs on an AT mega 328P (?), so you technically make one out of an arduino nano.... not that you'd want another thing to diagnose. With everything setup, I was having issues getting my GPS to connect to satellites, switching the parameter from auto to ublox (the brand of my gps) solved this.

I wanted to test my rover in manual mode first, before letting it drive itself around, and when doing this I encountered some very unusual behaviour. The rover would steer to the left when I increased the throttle, and steering would occasionally cause the throttle to go full backwards or fowards. I tried everything, including purchasing a new transmitter... and ended up just doing a full parameter reset, which fixed things. After this, I got super excited and decided to take the rover for its first auto drive, which didnt go very well. Before I sent it a new mission, The rover started freaking out, before trying to take off whilst setting the power supply on fire at the same time. This was not ideal, but I disarmed the rover and unplugged the dodgey cable as fast as I could. After this, the rover was acting fine, with the Pixhawk running off the ESC's power supply via the PWM output rail. This is not the reccomeneded way to power it, and I will purchase another power supply cable if need be. 



<i>The failed power supply cable</i>

After my little scare, I tried to get the auto mode working again, but just sitting in hold mode, the rover tried to reverse intermittently, which was not ideal. since with my current remote I don't have reverse anyway, I put the ESC in race mode, which disables reverse. This solved the problem. I was able to get the rover to drive up and down my driveway without issue, with relatively inaccurate gps signal it wasn't the most precise, but it works well enough for now,

I got the rover to drive up and down on our driveway in guided mode, which worked! I took this oppturnity to tune the rover a bit, and give it access to enough power to get up the hill.

## 23rd May

I decided to take the rover for a proper test run. There's a big oval not far from where I work, so Dad and I headed there after work to see how well things would work. I kinda expected something to fail but no, everything worked perfectly the first time, which never happens! I did a couple of guided, "fly to here commands to get an idea of how the rover would drive. I decided to up the throttle amount it could use from 30% to 50%, and this seemed to smooth things out. The turning radius is huge, so I want to spend some time tuning it. I gave the rover a set of waypoints to follow, and it did so with ease, all whilst keeping a pretty good gps track



<i>Don't worry, the satellite images are out of date. I did not trespass onto a construction site to test my rover</i>

In this image you can see the rover kinda swerves around on its way to the waypoint. This is due to the fact that I did absolutely zero compass calibration before the run, and the gps isn't quite mounted facing the right way. I think the rover actually did a very good job correcting for this. As we were doing our test runs towards the later end of the day (I got off work at 10pm) we resolved to attach a headtorch to the rover to act as "headlights". And maybe some tailights. and maybe some port/starboard lights.



<i>I should have taken a video...this will do for now</i>

There are two things I want to change

1. Obstacle avoidance. The rover was getting really close to crashing into me and my "base station". current ideas include ultrasonic (arduino sensor) or using my old Xbox kinect.
2. Isolating the environment from the guts of the rover. I managed to pick up every single grass clipping ever with my rover. This is not good.

## 31st May 

Between now and my last entry, I had to deal with a bunch of electrical gremlins. I wont go into detail, but basically, my Traxxas VXL-3S ESC did not want to play ball with my autopilot computer. Luckily for me, I had a spare, amazon special esc which worked fine. 

The next thing I wanted to do was to improve the mounting system. I made up some parts in fusion360. The idea with these was to make my mount alot stronger and less wobbly, reducing stress and enabling me to mount things better. 



I then 3d printed these pieces, one at a time due to the dubious reliablility of the 3d printers. I only got the first one done today, and the second one was completed about an hour after school finished, so I'll get another photo once both are finished.

  
  

Notice that the reciever and ESC just floating around in the car. My next plan is to make up a plate for them to mount to with doublesided tape. This will make things alot nicer.

I still havent gotten around to sorting out obstacle avoidance. That will come as soon as I can sort out all the other electronics first.

## 7th June 



This week, I finished printing the other mount and laser cut some cross braces. I built holes into the cross braces, that way I could mount the pixhawk and I also lowered the GPS. I was initially concerned about the GPS getting less reception due to being down lower, but in practice, this was not the case. I did have a display on the rover, but that has inexplicably ceased to work, so I don't know how many satellites... I think I can use ardupilot to give me a readout. 

I also mounted the speed controller and reciever much lower and properly wwith 3M DualLock velcro tape, which works really well.

After some brief testing, I found that I needed to make some mudguards to stop grass and mud entering the rover. I prototyped some parts out of cardboard, which worked pretty well and got rid of 99% of the debris, but the cardboard was not going to last very long, see below:




To fix this, I made some new parts out of coreflute. These look much cooler, and dont get saturated when used in water. I still have some water hitting the underside of the "cabin" portion of the body, and this can cause water to drip down into the "isloated" space where the electronics are, so I am going to look into getting a waterproof mesh cover or something similar. If I wanted everything totally waterproof, then I would probably put everything in a tuppawere container, but this is not a boat, so I should be fine. 




## 14th June 

I attempted to attach an FPV camera to the rover to give me a better idea of whats going on whilst I'm driving. I harvested this system off a cheap drone, and its supposedly 5.8Ghz. I did some brief tests, and the latency was really good. However, as soon as I got out into the field the range was actually abysmal

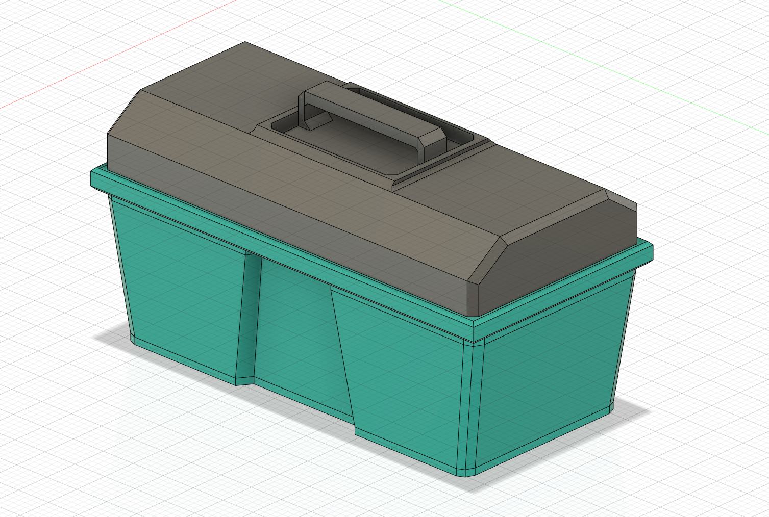
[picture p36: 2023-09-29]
journal/image.png

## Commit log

2023-04-02 Create Payload Clamp Prototype.f3d
    [Payload Clamp Prototype.f3d]
2023-04-04 Update CAD + add css
    Refined Clamp design via stress testing. Cosmetic improvement will follow shortly :)
    [Payload Clamp Prototype.f3d]
2023-04-04 Removed F3D file
    will upload barebones + final clamps as STL... eventually
    [Payload Clamp Prototype.f3d]
2023-04-10 Finished PAYLOAD.md Unitil I can prototype
2023-06-23 wip led bar classify
2023-09-28 Update ROVER.md
    LIDAR LB AND FW
